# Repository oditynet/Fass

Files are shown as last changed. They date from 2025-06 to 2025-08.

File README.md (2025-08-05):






### FASS 
Robot on Arduino and servos with 2 degrees of freedom.

### Status 
  **PROJECT IN DEVELOPMENT**

The robot can now: walk forward and backward, lift 1 paw/2 paws/4 paws up, down, sideways, receive commands via radio from the remote control, understands the distance from lidars. An algorithm for turning in a circle is currently being developed.

### Theory
(next information is very hard)
Forward and inverse kinematics:
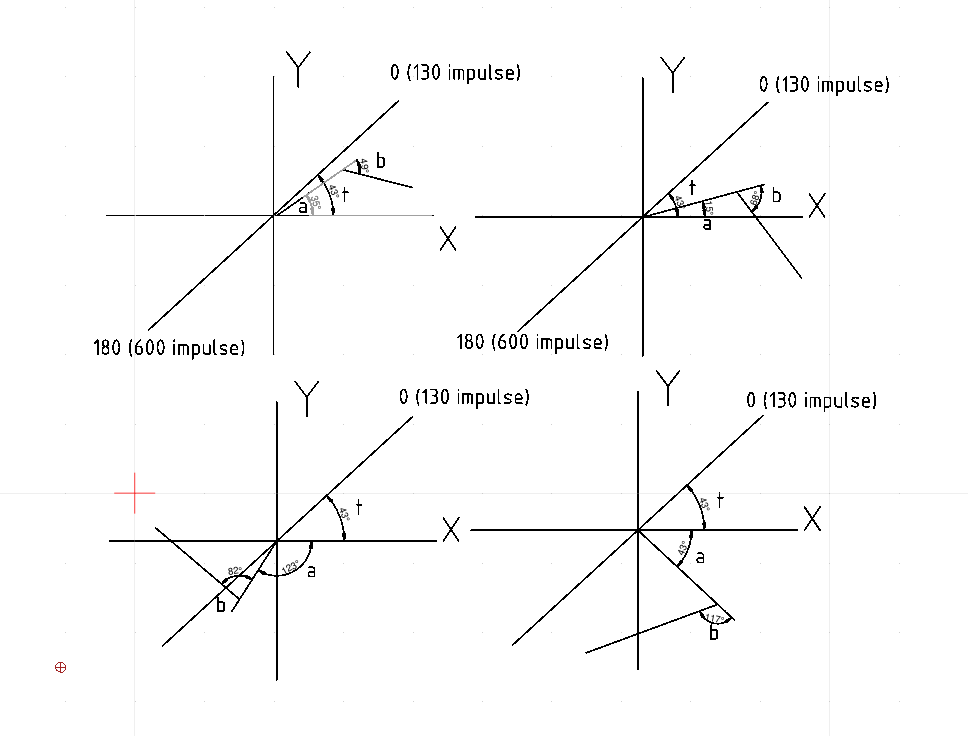
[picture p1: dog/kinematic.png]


Forward kinematics is knowing the impulses to find the coordinates of the end point X;Y.

For the first arm:

- x1 = L1 * cos(a);
- z1 = L1 * sin(a);

For the second arm. The minus sign is because the knee is pointing down and to get the second angle, you need to subtract from the first:

- x = x1 + L2 * cos((a - b));
- z = z1 + L2 * sin((a - b));

Inverse kinematics is to find angles (motor impulses) by X;Y coordinates. The graph shows 4 possible positions of the paw and therefore 4 different calculation methods. The angle t is always constant (equal to 45.5744 degrees), since the servo can rotate from 0 to 180 degrees (130 - 600 impulses) and for the motor this line is considered the abscissa. For the researcher, the abscissa is the X line. Arduino works with radians (1 rad = 57.29577 degrees) and therefore it is necessary to translate the values.

The same kinematics is for the movement of the paw to the side for turning. turning. walking sideways. The task is to find the angle y_c and to what height to compensate for the paw lift to the height z_H
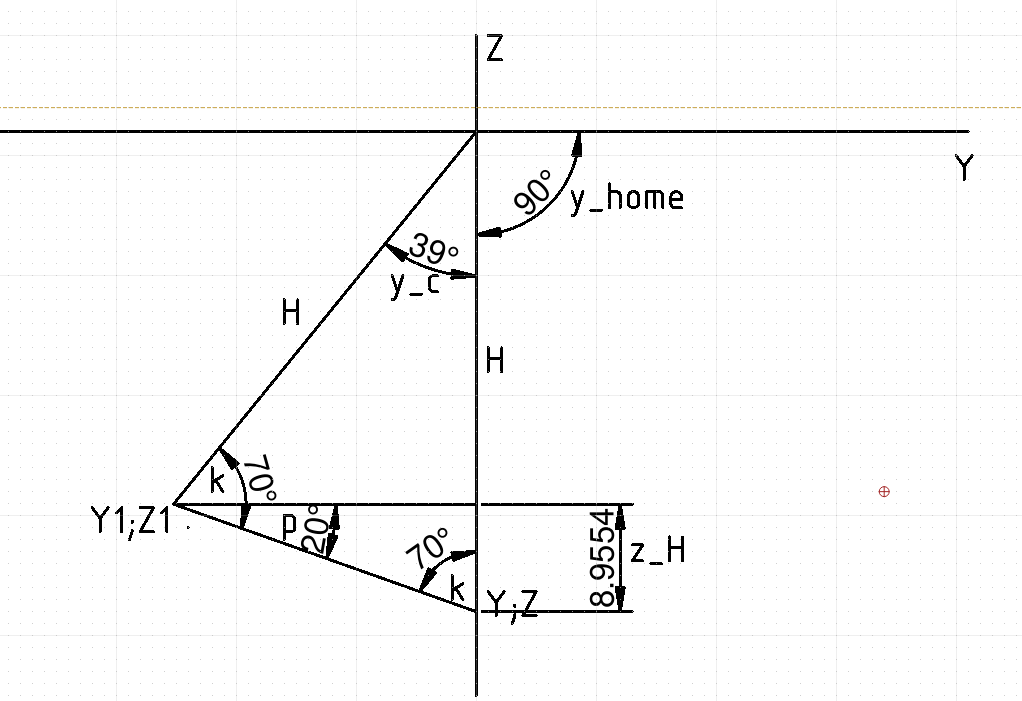
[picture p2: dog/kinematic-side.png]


### Step theory:

There are 2 types of steps in walking:

1) 2x2 - 1, 4 paws move forward at the same time and then 2, 3. The algorithm is successful when the dog's body is perfectly centered
2) 1x3 - the step cycle is divided into 4 stages (by the number of paws). The first paw moves forward in 1/4 of the period, and the other 3 continue to move backward. In the second period, 2/4, the second paw moves forward, and the others continue to move backward, and so on in a circle.

In my project, the center of gravity is unstable, so I chose option 2.

### HARDWARE LIST 
 1) Сервопривод SPT5435LV 35 кг                - 12 шт
 2) Понижающий регулятор напряжения на 10А     - 1 шт
 3) Arduino nano                               - 2 шт
 4) LM2596S-ADJ                                - 1 шт
 5) Подшипник фланцевый F688 ZZ                - 8 шт
 6) DS-212                                     - 5 шт
 7) KY-023                                     - 2 шт
 8) GY-521                                     - 1 шт
 9) HC-SR04                                    - 2 шт
 10) PCA9685                                   - 1 шт
 11) NRF24L01                                  - 2 шт
 12) LIPO 7.4V(ваш выбор) класс от 20С         - 2 шт
 13) болты и гайки M3                          - пакет на 100 шт

### Electrochema

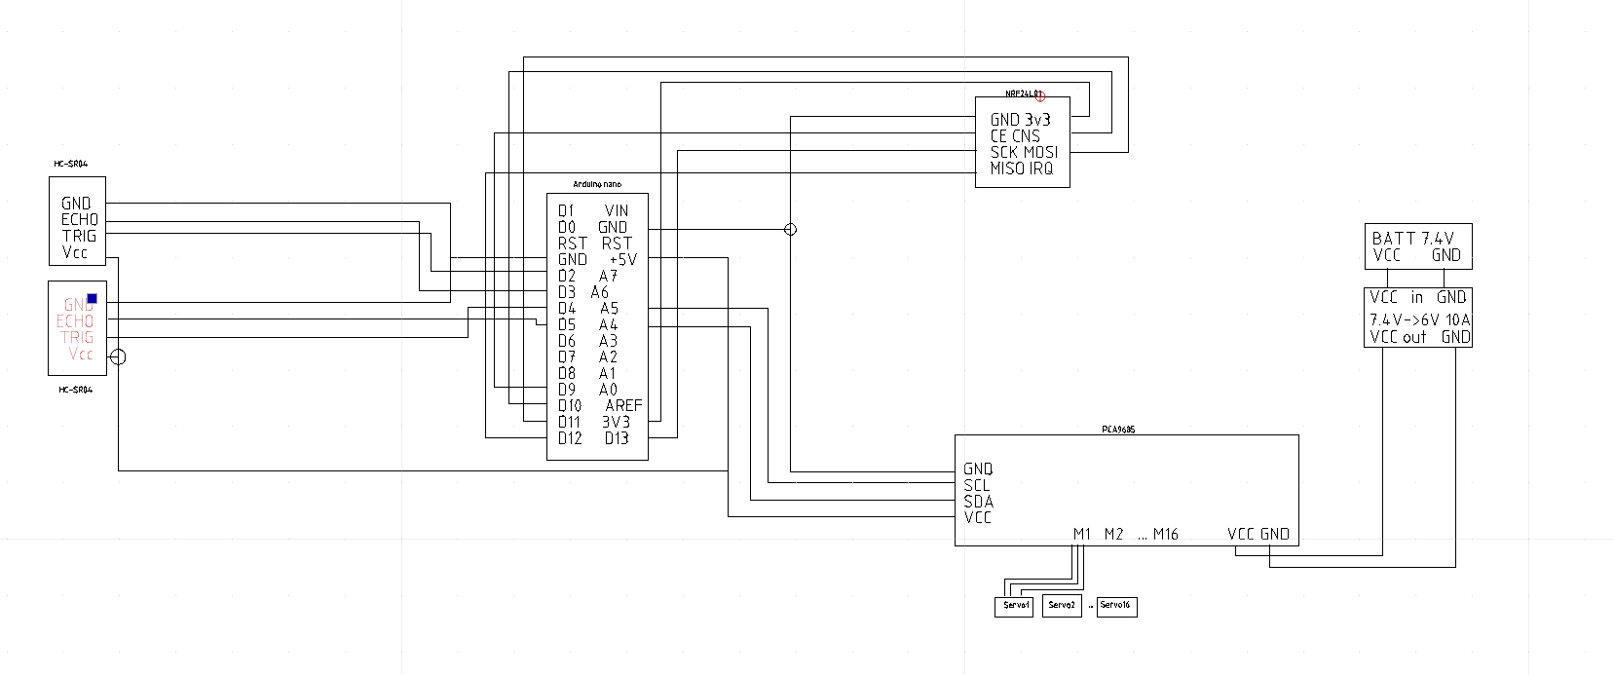
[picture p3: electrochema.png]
leg


### Video
  
Here is a video of the old kinematics motion logic. The new one works very accurately and takes into account all possible states.

leg

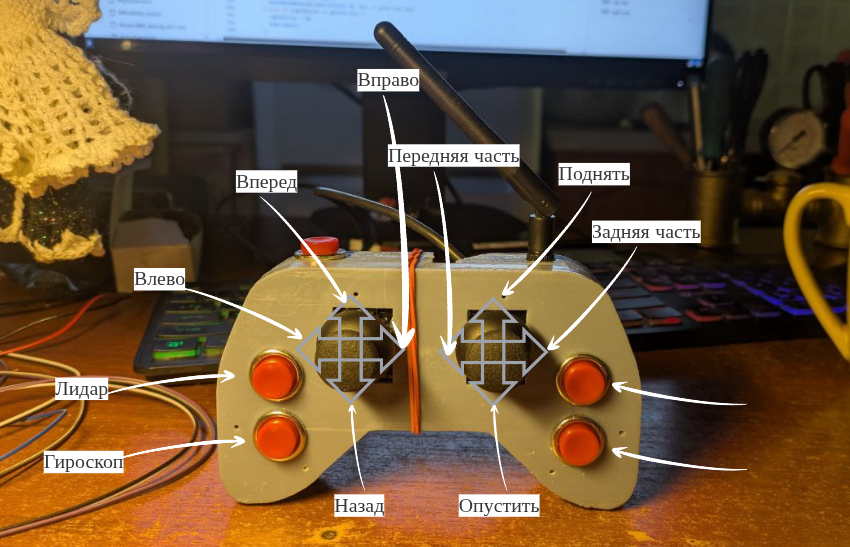
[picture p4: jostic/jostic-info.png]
jostic


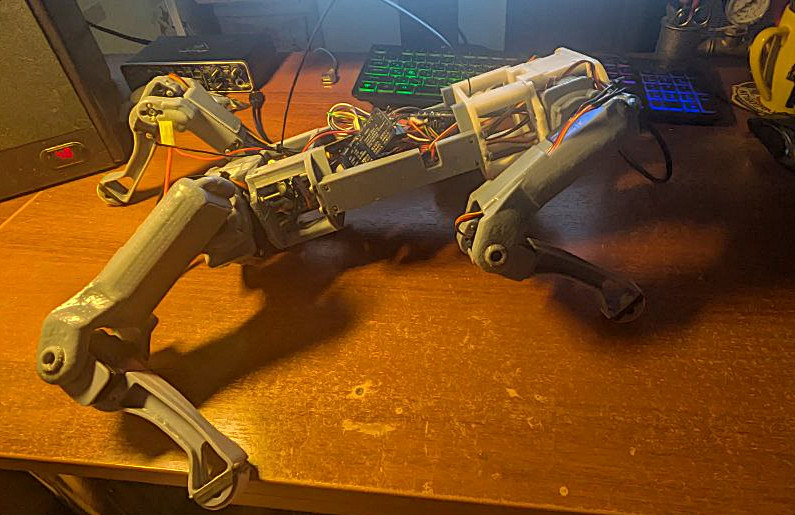
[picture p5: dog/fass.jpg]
fass


Main features of the implementation:
1) Control:
- Radio control via NRF24L01
- Automatic sensor priority
2) Movement algorithms:
- Smooth walking forward/backward
- Turns on the spot
- Automatic return to neutral position
- Adjustable movement speed
3) Inverse kinematics:
- Accurate calculation of joint angles
- Taking into account design constraints
- Smooth movement of legs
4) Safety system:
- Limiters for servos
- Smooth transitions between states

Hardware requirements:
- Arduino nano
- NRF24L01 module
- PCA9685 (servo driver)
- 12 servos (3 for each leg)
- MPU6050 (gyroscope / accelerometer)
- 2 HC-SR04 sensors (ultrasonic rangefinders)
- Remote control with two joysticks KY-023 and NRF24L01

origin project STL: https://novaspotmicro.com/parts-list.html with conversion to the metric system and my functionality. The software is written from scratch, inverse kinematics is developed and written from scratch. The algorithm is mine.

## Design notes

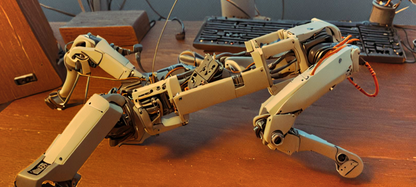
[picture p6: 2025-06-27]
head.png

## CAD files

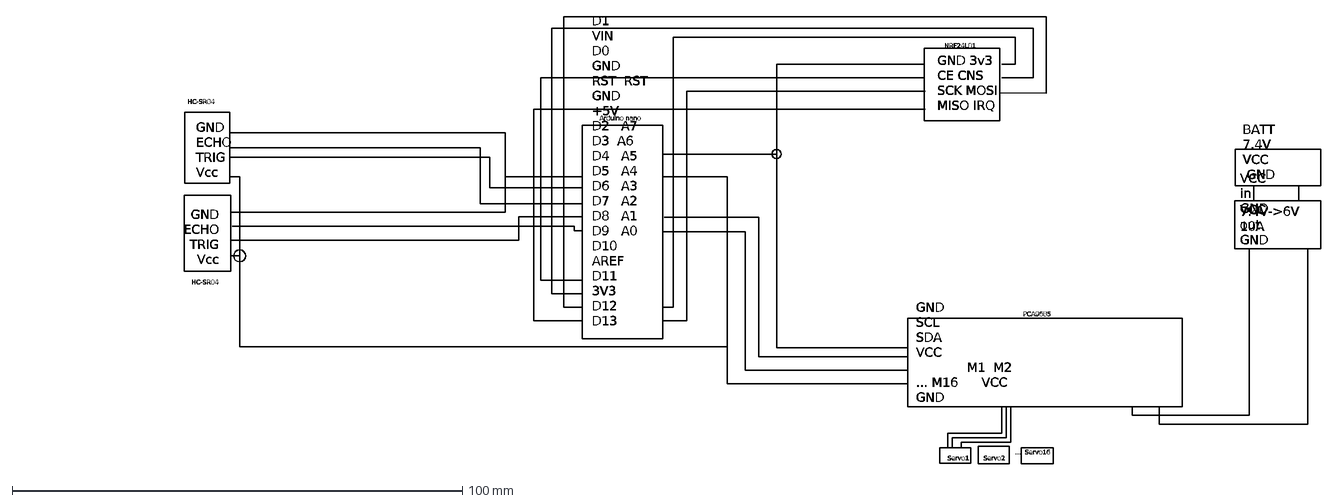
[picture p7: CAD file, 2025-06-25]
electrochema.dxf
D1\~\~\~ VIN D0\~ \~GND RST\~\~RST GND \~ +5V D2\~ \~A7 D3\~\~A6 D4\~ \~A5 D5\~ \~A4 D6\~ \~A3 D7\~ \~A2 D8\~ \~A1 D9\~ \~A0 D10\~ \~AREF D11\~ \~3V3 D12\~ \~D1
GND\~3v3 CE\~CNS SCK\~MOSI MISO\~IRQ
GND ECHO TRIG Vcc
GND SCL SDA VCC M1 M2 ... M16 VCC GND
Servo1
Servo2
... Servo16
BATT 7.4V VCC GND
7.4V->6V 10A
VCC in GND
VCC out GND
HC-SR04
Arduino nano
NRF24L01
PCA9685

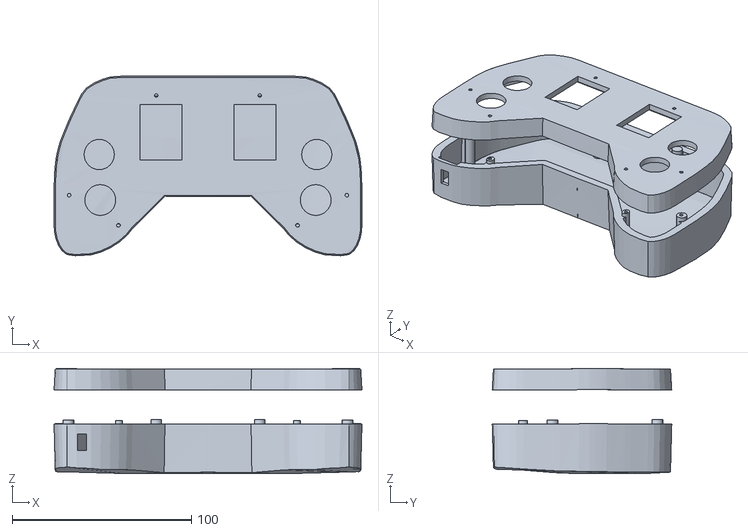
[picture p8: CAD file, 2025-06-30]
jostic/jostic-ver2.stl
171.7 x 100.1 x 58.6

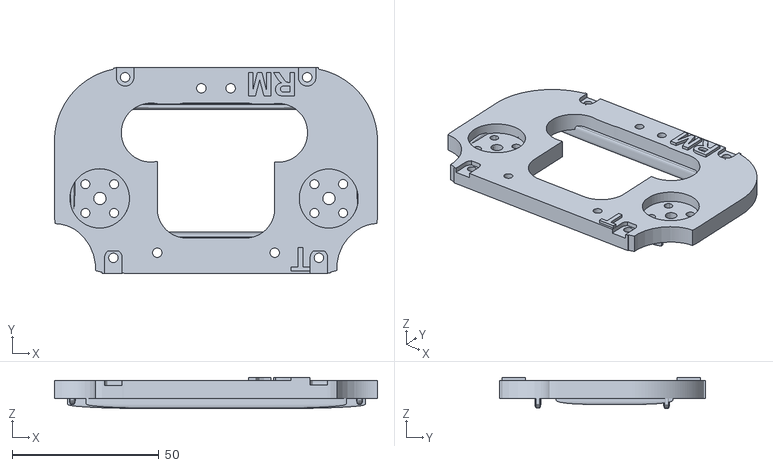
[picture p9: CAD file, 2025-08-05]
STL/G4-new.stl
110.0 x 70.0 x 10.6

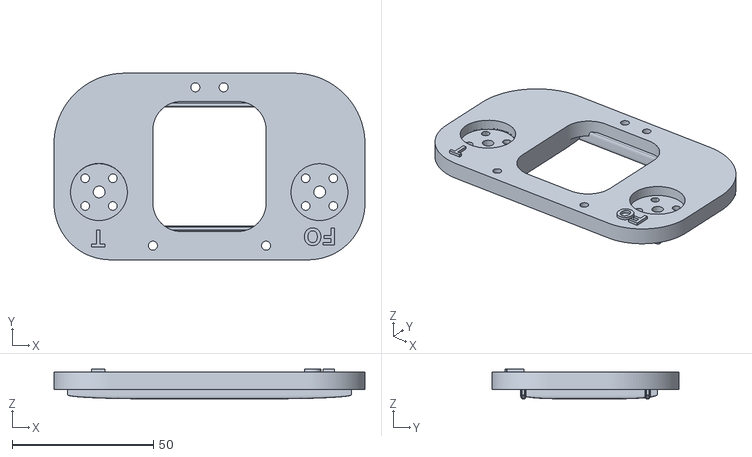
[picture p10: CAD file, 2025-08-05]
STL/G3-new.stl
110.0 x 66.0 x 10.5

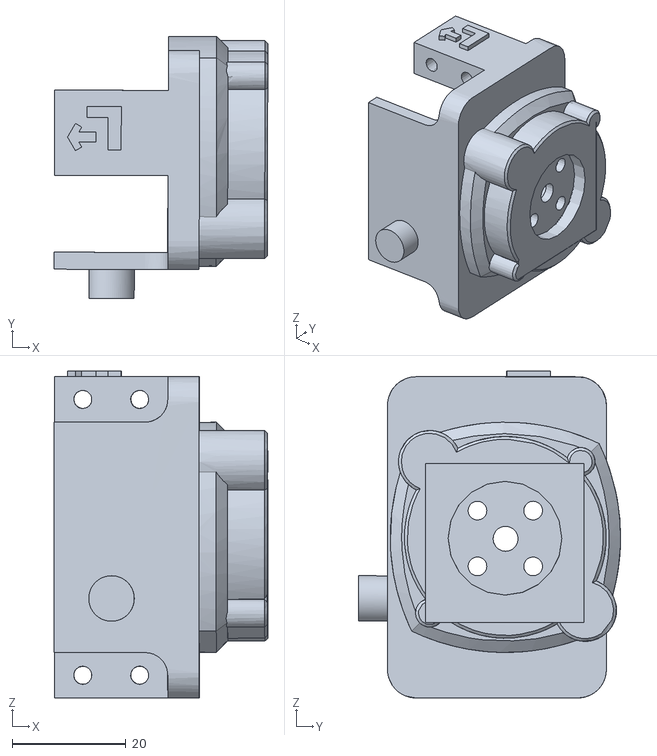
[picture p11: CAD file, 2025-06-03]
STL/SM3_Frame_LeftCoax-edit.stl
37.6 x 46.1 x 57.5

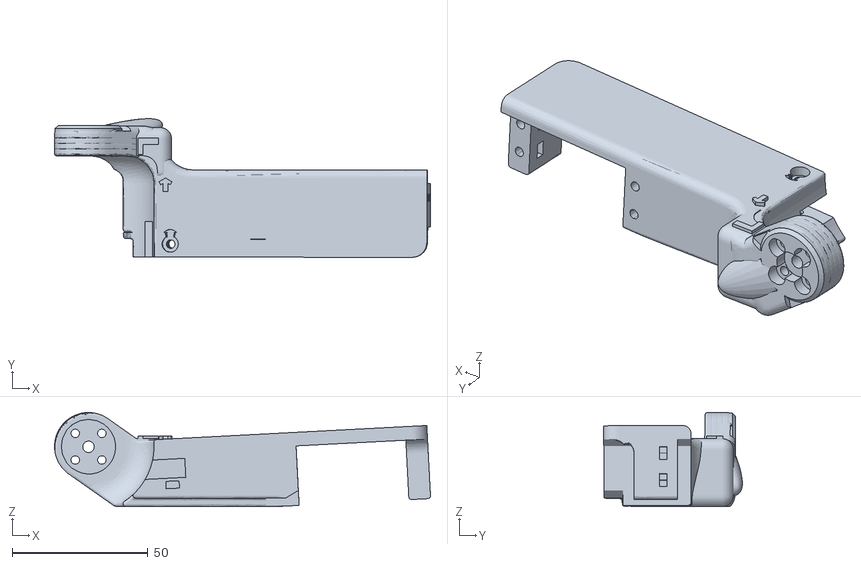
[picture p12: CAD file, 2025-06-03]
STL/SM3_Frame_LeftFemur-edit.stl
138.5 x 51.1 x 34.7

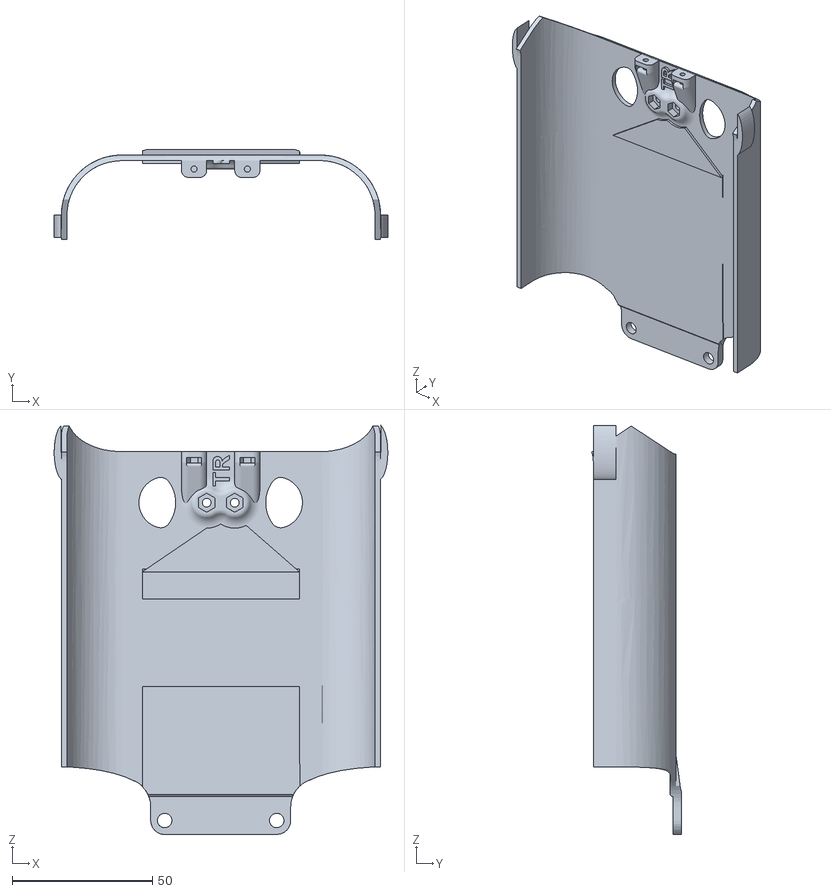
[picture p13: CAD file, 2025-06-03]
STL/SM3_Cover_TopRear.stl
119.1 x 32.1 x 146.0

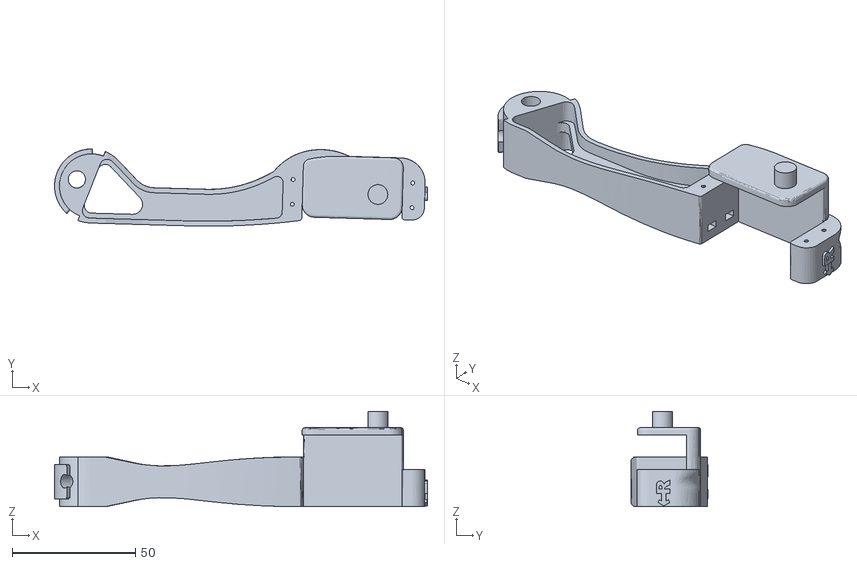
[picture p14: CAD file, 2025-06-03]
STL/SM3_Frame_RightTibia.stl
151.0 x 31.3 x 38.5

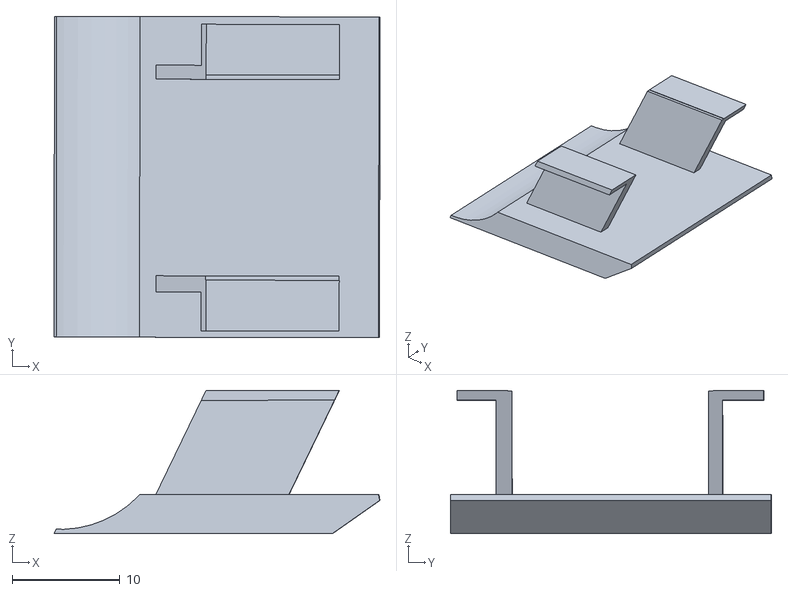
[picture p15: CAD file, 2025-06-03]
STL/SM3_Cover_HeadPanelSlug.stl
30.2 x 29.7 x 13.3

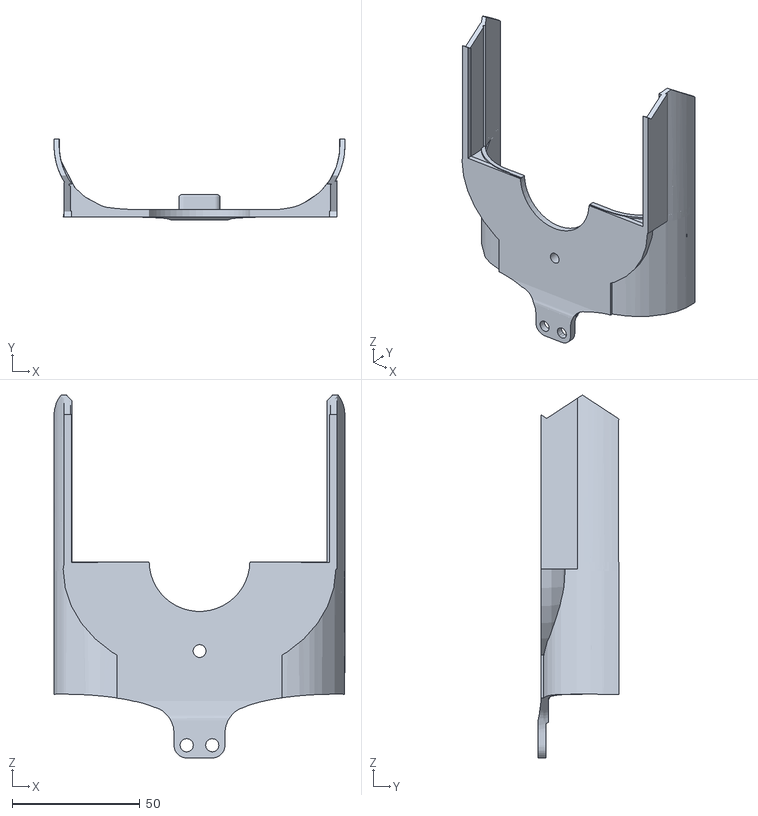
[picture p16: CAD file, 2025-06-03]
STL/SM3_Cover_BottomFront.stl
114.0 x 31.6 x 142.3

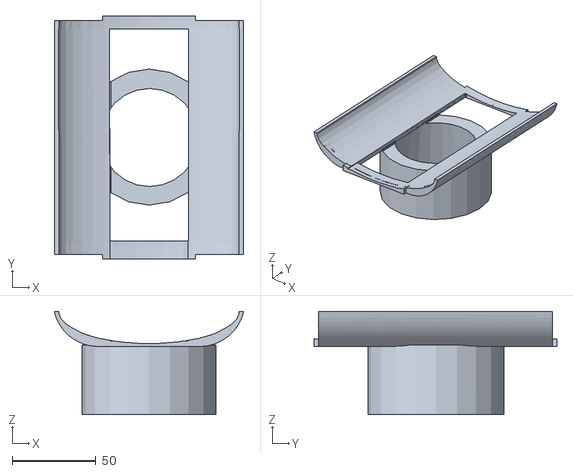
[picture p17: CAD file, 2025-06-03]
STL/SM3_Stand_ConeCap.stl
113.3 x 145.4 x 61.6

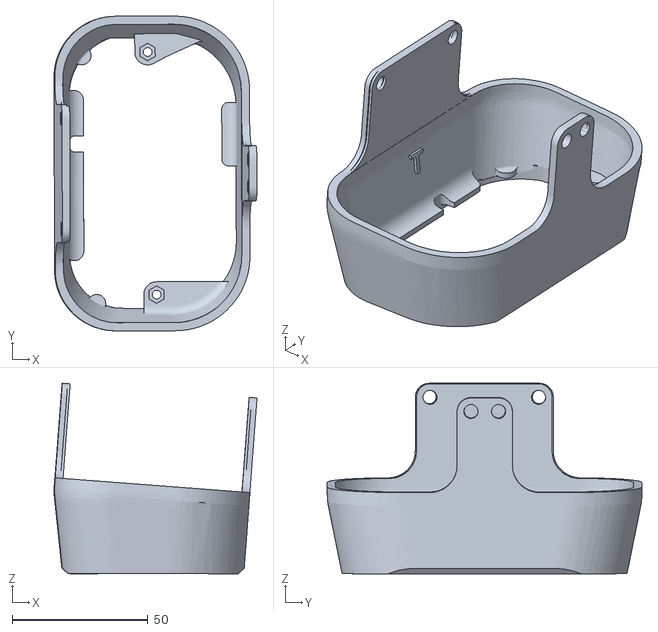
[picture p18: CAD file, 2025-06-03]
STL/SM3_Cover_RearPanel_2Piece_Shell.stl
74.8 x 116.1 x 70.2

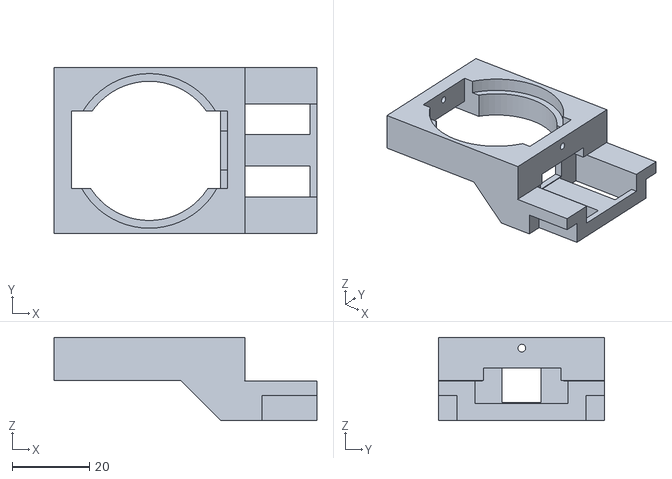
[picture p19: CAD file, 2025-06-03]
STL/SM3_Mp3ProSpeakerMount.stl
68.0 x 43.0 x 21.6

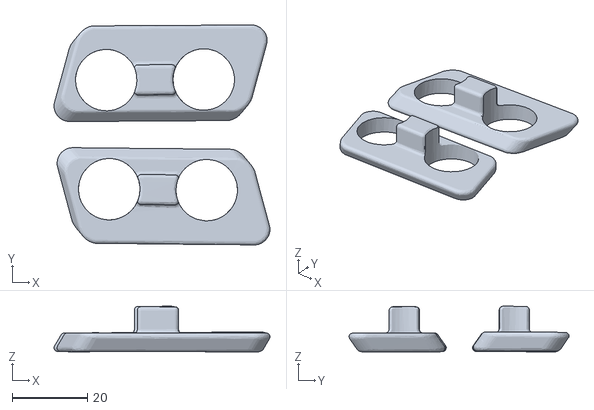
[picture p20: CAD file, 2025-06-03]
STL/SM3_Sensor_UltraSonicPlate.stl
57.6 x 58.6 x 12.2

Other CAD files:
STL/SM3_Cover_BottomHatch.stl
STL/SM3_Frame_FrontShoulderOuter.stl
STL/SM3_Sensor_PIRCup.stl
STL/SM3_Frame_FrontShoulderInner.stl
STL/SM3_Cover_BottomRear.stl
STL/SM3_Cover_LeftFemur.stl
STL/SM3_Cover_RearPanelBtnHolder_6x6LongBtn.stl
STL/SM3_Cover_RearPanel_2Piece_Base.stl
STL/SM3_Cover_RightFemur-edit.stl
STL/SM3_Cover_RightFemur.stl
STL/SM3_Cover_TopFront.stl
STL/SM3_Electronics_BuckConveterCase.stl
STL/SM3_Foot-edit.stl
STL/SM3_Foot.stl
STL/SM3_Frame_ChassisTrunk.stl
STL/SM3_Frame_FrontShoulderMiddle.stl
STL/SM3_Frame_LeftCoax.stl
STL/SM3_Frame_LeftFemur.stl
STL/SM3_Frame_LeftTibia.stl
STL/SM3_Frame_RearShoulderInner.stl
STL/SM3_Frame_RearShoulderMiddle.stl
STL/SM3_Frame_RearShoulderOuter.stl
STL/SM3_Frame_RightCoax.stl
STL/SM3_Frame_RightFemur.stl
STL/SM3_Sensor_FrontPIRMount.stl
STL/SM3_Sensor_MP3SpeakerMount.stl
STL/SM3_Sensor_RearPIRMount.stl
STL/SM3_Stand_ConeBase.stl

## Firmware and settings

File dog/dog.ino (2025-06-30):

//#include <Thread.h>  
#include <Wire.h>
#include <math.h>

#include <SPI.h>
#include <nRF24L01.h>
#include <RF24.h>

#include <Adafruit_PWMServoDriver.h>
Adafruit_PWMServoDriver pwm1 = Adafruit_PWMServoDriver();

#define TRIG1 2
#define ECHO1 3
#define TRIG2 5
#define ECHO2 4

// Конфигурация NRF24L01
#define CE_PIN   7
#define CSN_PIN 8


const byte thisSlaveAddress[4] = {'F','A','S','S'};
RF24 radio(CE_PIN, CSN_PIN);

// Структура для данных с пульта
struct RemoteData {
  int leftX;
  int leftY;
  int rightX;
  int rightY;
  int btn1;
  int btn2;
  int btn3;
  int btn4;
  int checksum; // Добавляем поле для контрольной суммы
};


//int spd = 50;

int L0 = 38;
int L1 = 108;
int L2 = 130;

int Lbody = 280;
int gotohome=0;

// Конфигурация сервоприводов
const int NUM_LEGS = 4;
const int NUM_JOINTS_PER_LEG = 3; // Плечо, бедро, колено
//const int FL = 0, FR = 1, RL = 2, RR = 3; // Индексы ног
//const int SHOULDER = 0, HIP = 1, KNEE = 2; // Индексы суставов

const int STEP_LENGTH = 40; //длина шага
const int STEP_HEIGHT = 30; //высота шага

//unsigned long previousMillis = 0;  // время хранения loop
//const long loop_interval = 500; // время проверки данных с джостика

const int legs[4][3][4] = {
  {{0, 130 ,600, 353}, {1, 130 ,600, 400}, {2,130, 600, 345}},   // FL плечо,бедро,локоть    
  {{4, 130 ,600, 335}, {5, 600 ,130, 347}, {6,600, 130, 379}},   // FR
  {{8, 130 ,600, 370}, {9, 130 ,600, 350}, {10,130, 600, 360}},   // RL
  {{12, 130 ,600, 372}, {13, 600 ,130, 385}, {14,600, 130, 360}}    // RR
};

float legspos[4][4] = { //X, Z, Height, Y
  {0, 0, 220, 0},  // FL   200 - примерно. надо вычислить home высоту TODO 
  {0, 0, 220, 0},  // FR
  {0, 0, 220, 0},  // RL
  {0, 0, 220, 0}   // RR
};

//Thread gefromjosticdata = Thread();

void step4legstoside(bool left, float STEP_DURATION, int Rcentr = 200);

float getDistance(int trigPin, int echoPin) {
  // Генерируем импульс 10 мкс
  digitalWrite(trigPin, LOW);
  delayMicroseconds(2);
  digitalWrite(trigPin, HIGH);
  delayMicroseconds(10);
  digitalWrite(trigPin, LOW);
  
  // Измеряем длительность импульса
  long duration = pulseIn(echoPin, HIGH);
  
  // Рассчитываем расстояние (см)
  //return duration * 0.034 / 2;
   return duration / 58;
}

int inverseLinearTransform(int value, int inMin = 0, int inMax = 400, int outMin = 200, int outMax = 1000) {
    // Ограничиваем входное значение в диапазоне [inMin, inMax]
    value = constrain(value, inMin, inMax);
    
    // Вычисляем преобразование с обратной линейностью
    return map(value, inMin, inMax, outMin, outMax);
}

void processRemoteData(RemoteData data) {
  // Движение вперед/назад/повороты
  int value;
  if (data.leftY < 400) {
    Serial.print("Y_up: "); Serial.println(data.leftY);

    value = inverseLinearTransform(data.leftY);
    gotohome=1;
    stepalllegs(false,value, 0 ); 
  } else if (data.leftY > 600) {
    Serial.print("Y_down: "); Serial.println(data.leftY);

    value = inverseLinearTransform(data.leftY, 600, 1024);
    gotohome=1;
    stepalllegs(true,value,0);
  } else if (data.leftX < 400) {
    Serial.print("X_up: "); Serial.println(data.leftX);

    value = inverseLinearTransform(data.leftX,0,400,1,40);
    gotohome=1;
    heightchange4leg(value); //LEft
  } else if (data.leftX > 600) {
    Serial.print("X_donwn: "); Serial.println(data.leftX);

    value = inverseLinearTransform(data.leftX,600, 1024, -1, -40);
    gotohome=1;
    heightchange4leg(value);//right
  } else if (abs(data.leftX - 512) < 100 && abs(data.leftY - 512) < 100) {
    
    if (gotohome == 1){
      Serial.println("Home: "); 
      //gohome();
      gotohome=0;
    }
  }
  if (data.rightX < 400) {
    Serial.print("R X_left: "); Serial.println(data.rightX);

    value = inverseLinearTransform(data.rightX);
    gotohome=1;
    step4legstoside(true, value); // Влево
  } else if (data.rightX > 600) {
    Serial.print("R X_right: "); Serial.println(data.rightX);
  
    value = inverseLinearTransform(data.rightX,600, 1024);
    gotohome=1;
    step4legstoside(false,  value); // Вправо
  }
}

void readRemoteData() {
  if (radio.available()) {
    RemoteData data;

    radio.read(&data, sizeof(data));

    int calculatedChecksum = data.checksum = data.leftX +data.leftY +data.rightX +data.rightY +data.btn1+data.btn2+data.btn3+data.btn4;
    if (data.checksum == calculatedChecksum && calculatedChecksum != 0) {
      
      Serial.println("Received raw data:");
      Serial.print("LX: "); Serial.print(data.leftX);
      Serial.print(" LY: "); Serial.print(data.leftY);
      Serial.print(" RX: "); Serial.print(data.rightX);
      Serial.print(" RY: "); Serial.print(data.rightY);
      Serial.print(" BTN: "); Serial.print(data.btn1);
      Serial.print(","); Serial.print(data.btn2);
      Serial.print(","); Serial.print(data.btn3);
      Serial.print(","); Serial.print(data.btn4);
      Serial.print(" Checksum: "); Serial.println(data.checksum);
      
      processRemoteData(data);
    }
  }
}

double realangleToPulse(double angle, int minPulse, int maxPulse, double minAngle = 0, double maxAngle = 180) {
    if (minPulse > maxPulse) {
        return maxPulse + (minPulse - maxPulse) * (1 - angle/180.0);
    }
    return minPulse + (maxPulse - minPulse) * (angle/180.0);
}

// Преобразование импульса в угол с учетом реального диапазона
double realpulseToAngle(int pulse, int minPulse, int maxPulse, double minAngle = 0, double maxAngle = 180) { 
    if (minPulse > maxPulse) {
        return 180.0 - 180.0 * (pulse - maxPulse) / (minPulse - maxPulse);
    }
    return 180.0 * (pulse - minPulse) / (maxPulse - minPulse);
}

void forwardKinematics(int leg,int hipPulse, int kneePulse, double &x, double &z) {
  double b = realpulseToAngle(kneePulse, legs[leg][2][1], legs[leg][2][2]);
  double a = realpulseToAngle(hipPulse, legs[leg][1][1], legs[leg][1][2]);

  //Serial.print("a=");Serial.print(a);Serial.print(" b=");Serial.println(b);
  //double P1 = (600-130)/180; //1 пульс = 2,61 градусам

  double b_Rad = radians(b);
  double a_Rad = radians(a);
  double x1,z1;
  
  a_Rad = radians(45.5744 - a);
  x1 = L1 * cos(a_Rad);
  z1 = L1 * sin(a_Rad);
  
  x = x1 + L2 * cos((a_Rad - b_Rad));
  z = z1 + L2 * sin((a_Rad - b_Rad));
  /*Serial.print("leg ");Serial.print(leg);
  Serial.print(" x1="); Serial.print(x1);
  Serial.print(" z1="); Serial.print(z1);
  Serial.print(" x=");  Serial.print(x); Serial.print(" z="); Serial.println(z);*/
}

bool inverseKinematics(int leg, double X, double Z, int &hipPulse, int &kneePulse) {
  double D = sqrt(X*X+Z*Z);
 // Serial.print("D=");Serial.println(D);
  if (D > L1 + L2 || D < abs(L1 - L2)) {
        Serial.println("Точка недостижима");
        return false;
  }
  double a,b,g,t,k;
  double _const =  45.5744;//(180/(600-130)) * (249-130);
  double MM_PI = 3.1415926;
  b = MM_PI - acos((L2*L2+L1*L1-D*D)/(2*L2*L1));

  if (X >= 0 && Z <= 0){ // 1 случай
   // Serial.println("[2]");
    t=acos((L1*L1-L2*L2+D*D)/(2*L1*D));
    k=acos(abs(X)/D);
    a = k-t+_const/57.29577; //+
  }
  else if (X >= 0 && Z >= 0){
    //Serial.println("[1]");
    k = acos(X/D);
    t = acos((L1*L1+D*D-L2*L2)/(2*L1*D));
    a = abs(_const/57.29577 - k - t);  //+
  }
  else if (X <= 0 && Z >= 0){
    //Serial.println("[4]");
    //a = MM_PI - acos((D*D + L1*L1 - L2*L2)/(2*L1*D)); //TODO кажется неверно ищится,т.к. весь треугольник не надо учитывать,раз у нас есть линия по 600 имп.
    a = /*90 гр перевел в рад*/1.57079632679 + (acos(abs(X)/D)) -  acos((D*D + L1*L1 - L2*L2)/(2*L1*D)); // перепроверить надо!!!!!
  }
  else if (X <= 0 && Z <= 0){
    //Serial.println("[3]");//Serial.println(MM_PI);Serial.println(PI);
    double k = acos(abs(X)/D);
    if (k * 57.29577 >= _const ) {// гр > гр
      //Serial.println("[3_1]");
     // Serial.println(k * 57.29577);
      a = MM_PI - (acos(abs(X)/D) - _const/57.29577) - acos((D*D + L1*L1 - L2*L2)/(2*L1*D));
    }else{
      //Serial.println("[3_2]");
      double kk = asin(abs(Z)/D);
      //a = kk-0.77537299217 ;
      a = MM_PI - (acos((D*D + L1*L1 - L2*L2)/(2*L1*D)) - kk + 0.77537299217); /*(90-45гр и в радианы перевел)*/
    }
    //double tmp = _const / 57.29577;
    //a = MM_PI - (acos(abs(X)/D) - (90 - _const)/57.29577) - acos((D*D + L1*L1 - L2*L2)/(2*L1*D));
    /*double theta = atan2(abs(X), abs(Z)); // Угол от отрицательной оси Z
    double cosGamma = (D*D + L1*L1 - L2*L2) / (2*L1*D);
    double gamma = acos(cosGamma);
    a = theta - gamma + _const/57.29577;*/
    //a = /*90 гр перевел в рад*/1.57079632679 + (acos(abs(X)/D)) -  acos((D*D + L1*L1 - L2*L2)/(2*L1*D));
  }
  else{
    Serial.println("[!] Not calculate");
    return false;
  }
  /*Serial.println("угол: ");
  Serial.println(a*57.29577);
  Serial.println(b*57.29577);
  */
  double rad_a = degrees(a);//-0.795423467); // это 45.5744 градусов
  double rad_b = degrees(b);

  kneePulse = realangleToPulse(rad_b, legs[leg][2][1], legs[leg][2][2]);
  hipPulse = realangleToPulse(rad_a, legs[leg][1][1], legs[leg][1][2]);
  return true;
}

void move1Leg(bool forward,int STEP_DURATION,double STEP_LENGTH,double STEP_HEIGHT , int servnum1, int servnum2 , int homeX, int homeZ,int leg) {

  const int NUM_STEPS = 25;        // Количество промежуточных точек
  double x,z;
  for (int i = 0; i <= NUM_STEPS; i++) {
    double t = (double)i / NUM_STEPS;
    
    // Фаза переноса (ПОДЪЕМ ноги)
    if (forward) {
      x = homeX + STEP_LENGTH * (1 - cos(PI * t)) ;
    } else {
      x = homeX - STEP_LENGTH * (1 - cos(PI * t)) ;
    }
    z = homeZ + STEP_HEIGHT * sin(PI * t); 
    
    // Отладочный вывод
    /*Serial.print("Target: X="); Serial.print(x);
    Serial.print(" Z="); Serial.println(z);
    moveToPoint(leg,x,z,servnum1,servnum2);*/

    delay(STEP_DURATION / (2 * NUM_STEPS));
  }
  double tmp;
  if (x > homeX) {
    tmp =  x - homeX;
  } else {
    tmp = homeX - x;
  }
  //2 фаза: возврат назад
  for (int i = 0; i <= NUM_STEPS; i++) {
   
    if (forward) {
      x = x - tmp / NUM_STEPS;
    } else {
      x = x + tmp / NUM_STEPS; 
    }

   /* Serial.print("Target: X="); Serial.print(x);
    Serial.print(" Z="); Serial.println(z);
*/
    moveToPoint(leg,x,z,servnum1,servnum2);
    delay(STEP_DURATION / (2 * NUM_STEPS));
  }
}

bool moveToPoint(int leg,double targetX, double targetZ, int servnum1, int servnum2 ) {
  int hipPulse, kneePulse;

 // Serial.println(targetZ);
  
  if (inverseKinematics(leg,targetX, targetZ, hipPulse, kneePulse)) {
    // Управление сервоприводами
    pwm1.setPWM(servnum1, 0, hipPulse);
    pwm1.setPWM(servnum2, 0, kneePulse);
    return true;
  } else {
    Serial.println("Ошибка перемещения");
  }
  return false;
}


void stepalllegs(bool forward,int speed, int left){ // left ^ 0- forward, 1- left, 2- right
 /* if (left == 1 || left ==0 ){
    step2legs(forward,0,3, legspos[0][0], legspos[0][1], legspos[3][0], legspos[3][1], speed); //
    step2legs(forward,1,2, legspos[1][0], legspos[1][1], legspos[2][0], legspos[2][1], speed); // поворот налево только
  }
  if (left == 1 || left == 0){
    step2legs(forward,1,2, legspos[1][0], legspos[1][1], legspos[2][0], legspos[2][1], speed);
    step2legs(forward,0,3, legspos[0][0], legspos[0][1], legspos[3][0], legspos[3][1], speed); 
  }*/
}
/*
void step2legs(bool forward, int legF, int legR, int homeX, int homeZ, int homeX1, int homeZ1,int STEP_DURATION){
  const int NUM_STEPS = 30;        // Количество промежуточных точек
  const int delta = 2;        // Разница можду шагаме переда и зада
  double x,z,x1,z1, t, t1;
  for (int i = 0; i <= NUM_STEPS+delta; i++) {
    if (i<= NUM_STEPS){
      t = (double)i / NUM_STEPS;

      if (forward) {
        x = homeX + STEP_LENGTH * (1 - cos(PI * t)) / 2;
      } else {
        x = homeX - STEP_LENGTH * (1 - cos(PI * t)) / 2;
      }
      z = homeZ + STEP_HEIGHT * sin(PI * t)/2; 
      moveToPoint(legF, x, z , legs[legF][1][0] , legs[legF][2][0]);

      legspos[legF][0] = x;
      legspos[legF][1] = z;
    }
    if (i >= delta){
      t1 = (double)(i-delta) / NUM_STEPS;

      if (forward) {
        x1 = homeX1 + STEP_LENGTH * (1 - cos(PI * t1)) / 2;
      } else {
        x1 = homeX1 - STEP_LENGTH * (1 - cos(PI * t1)) / 2;
      }
      z1 = homeZ1 + STEP_HEIGHT * sin(PI * t1)/2; 

      moveToPoint(legR, x1, z1 , legs[legR][1][0] , legs[legR][2][0]);
      
      legspos[legR][0] = x1;
      legspos[legR][1] = z1;
    }
    delay(STEP_DURATION / (2 * NUM_STEPS));
  }
  double tmp;
  if (x > homeX) {
    tmp =  x - homeX;
  } else {
    tmp = homeX - x;
  }
  //2 фаза: возврат назад
  for (int i = 0; i <= NUM_STEPS; i++) {
   
    if (forward) {
      x = x - tmp / NUM_STEPS;
    } else {
      x = x + tmp / NUM_STEPS; 
    }
    moveToPoint(x,z);
    delay(STEP_DURATION / (2 * NUM_STEPS));
  }
}
*/
int changeleg(int leg) {
    const int nextLeg[] = {2, 3, 1, 0}; // 0->2, 1->3, 2->1, 3->0
    return nextLeg[leg];
}
int changeleg0312(int leg) {
    const int nextLeg[] = {3, 2, 0, 1}; // 0->2, 1->3, 2->1, 3->0
    return nextLeg[leg];
}

void step4legs(bool forward, int STEP_DURATION, int len4step = 150) {
    const int NUM_SECTIONS = 4;
    const int STEPS_PER_SECTION = 10; // Фиксированное количество шагов на секцию
    const float SECTION_DURATION = STEP_DURATION / (float)NUM_SECTIONS;
    const float TIME_PER_STEP = SECTION_DURATION / STEPS_PER_SECTION;
    const float SECTION_LENGTH = len4step / (float)NUM_SECTIONS;

    int active_leg = 0; // Начинаем с ноги 0
    float start_positions[4][2]; // Стартовые позиции для всех ног

    for (int section = 0; section < NUM_SECTIONS; section++) {
        // Сохраняем стартовые позиции для всех ног
        for (int l = 0; l < 4; l++) {
            start_positions[l][0] = legspos[l][0];
            start_positions[l][1] = legspos[l][1];
        }

        for (int step = 0; step <= STEPS_PER_SECTION; step++) {
            float t = (float)step / STEPS_PER_SECTION; // Прогресс [0, 1]

            // Обработка ВСЕХ ног
            for (int l = 0; l < 4; l++) {
                if (l == active_leg) {
                    // Траектория активной ноги (полуэллипс)
                    float x, z;
                    if (forward) {
                        x = start_positions[l][0] + SECTION_LENGTH * t;
                    } else {
                        x = start_positions[l][0] - SECTION_LENGTH * t;
                    }
                    z = start_positions[l][1] + STEP_HEIGHT * sin(PI * t);
                    moveToPoint(l, x, z, legs[l][1][0], legs[l][2][0]);
                    legspos[l][0] = x;
                    legspos[l][1] = z;
                    delay(TIME_PER_STEP/(4*10));//быстрее
                } else {
                    // Траектория опорных ног (прямая с компенсацией)
                    float compensation = (forward ? -1 : 1) * SECTION_LENGTH * t / 3.0f;
                    float x = start_positions[l][0] + compensation;
                    moveToPoint(l, x, start_positions[l][1], legs[l][1][0], legs[l][2][0]);
                    // Не обновляем legspos здесь - только в конце секции
                    delay(TIME_PER_STEP/4);
                }
            }
            //delay(TIME_PER_STEP);
        }

        // Финализируем позиции после секции
        for (int l = 0; l < 4; l++) {
            if (l != active_leg) {
                float compensation = (forward ? -1 : 1) * SECTION_LENGTH / 3.0f;
                legspos[l][0] = start_positions[l][0] + compensation;
            }
        }

        // Логирование после каждой секции
        Serial.print("End section ");
        Serial.print(section);
        Serial.print(" - ");
        for (int l = 0; l < 4; l++) {
            Serial.print("Leg");
            Serial.print(l);
            Serial.print(": ");
            Serial.print(legspos[l][0]);
            Serial.print(" ");
        }
        Serial.println();

        // Переключаем активную ногу
        active_leg = changeleg(active_leg);
    }
}

void step1legtoside(bool left, int leg,int len){  // work!!
  double ab = (left ? 1 : -1)*(atan(len/abs(legspos[leg][1])) + atan((L1+L2)/L0));
  Serial.println(ab);
  //double rad_ab = degrees(ab);
  double shoulder = realangleToPulse(degrees(ab), legs[leg][0][1], legs[leg][0][2]);// +(left ? 1 : -1)*legs[leg][0][3];
  Serial.println(shoulder);
  pwm1.setPWM(legs[leg][0][0], 0, shoulder);
}
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
void loop() {

  //for (int i=0;i< 10;i++){
  //step4legstoside(true, 1000); 
  //}
  //gohome();
  readRemoteData();
  delay(500);

  /*float dist1 = getDistance(TRIG1, ECHO1);
  float dist2 = getDistance(TRIG2, ECHO2);
  Serial.print("Left: ");
  Serial.print(dist1);
  Serial.print(" cm | Right: ");
  Serial.print(dist2);
  Serial.println(" cm");
  delay(200);
*/
  /*for (int i=0;i< 10;i++){
  delay(7);
  step4legs(false,700); // технология 1х3
  }
  for (int i=0;i< 10;i++){
  delay(7);
  step4legs(false,400); // технология 1х3
  }
  for (int i=0;i< 10;i++){
  delay(7);
  step4legs(false,200); // технология 1х3
  }*/
  //stepalllegs(false,1000,0); // технология 2х2
//move1Leg(false,30,80,40 ,5,6 , legspos[3][0], legspos[3][1],3);
  //if (gefromjosticdata.shouldRun())
   //     gefromjosticdata.run();
  /*  АНАЛОГ
  unsigned long currentMillis = millis(); 
  if (currentMillis - previousMillis >= loop_interval){
     previousMillis = currentMillis;
     // чтение данных с джостика
  }*/
  

}

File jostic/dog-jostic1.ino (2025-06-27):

#include <SPI.h>
#include <nRF24L01.h>
#include <RF24.h>

// Конфигурация NRF24L01
#define CE_PIN   7
#define CSN_PIN 8
const byte slaveAddress[4] = {'F','A','S','S'};
RF24 radio(CE_PIN, CSN_PIN); // Create a Radio

// Пины джойстиков
const int LEFT_JOYSTICK_X = A2;
const int LEFT_JOYSTICK_Y = A3;
const int RIGHT_JOYSTICK_X = A0;
const int RIGHT_JOYSTICK_Y = A1;

struct RemoteData {
  int leftX;
  int leftY;
  int rightX;
  int rightY;
  int btn1;
  int btn2;
  int btn3;
  int btn4;
  int checksum; // Добавляем поле для контрольной суммы
};

// Параметры калибровки
const int NEUTRAL_ZONE = 50;  // Зона нечувствительности
const int MIN_THRESHOLD = 400; // Нижний порог активации
const int MAX_THRESHOLD = 600; // Верхний порог активации

const int button1 = 3;
const int button2 = 2;
const int button3 = 6;
const int button4 = 5;

// Таймер для отправки данных
unsigned long lastSendTime = 0;
const int SEND_INTERVAL = 500; // Интервал отправки (мс)

void setup() {
  Serial.begin(115200);
  Serial.println("Инициализация пульта управления...");
  
  // Настройка пинов джойстиков
  pinMode(LEFT_JOYSTICK_X, INPUT);
  pinMode(LEFT_JOYSTICK_Y, INPUT);
  pinMode(RIGHT_JOYSTICK_X, INPUT);
  pinMode(RIGHT_JOYSTICK_Y, INPUT);

    radio.begin();
    radio.setDataRate( RF24_250KBPS );
    //radio.setRetries(1,1); // delay, count
    radio.openWritingPipe(slaveAddress);
    radio.setChannel(98);
     radio.setAutoAck(true);
  
  while (!radio.isChipConnected()) {
    Serial.println("Ошибка: nRF24L01 не подключен!");
    delay(1000);
  }
  
  pinMode(button1, INPUT_PULLUP);
  pinMode(button2, INPUT_PULLUP);
  pinMode(button3, INPUT_PULLUP);
  pinMode(button4, INPUT_PULLUP);

  Serial.println("Пульт готов к работе");
}

void loop() {
  // Чтение значений с джойстиков
  RemoteData data;
  
  // Отправка данных с заданным интервалом
  if (millis() - lastSendTime >= SEND_INTERVAL) {
    data.leftX = analogRead(LEFT_JOYSTICK_X);
    data.leftY = analogRead(LEFT_JOYSTICK_Y);
    data.rightX = analogRead(RIGHT_JOYSTICK_X);
    data.rightY = analogRead(RIGHT_JOYSTICK_Y);
    

    data.btn1 = !digitalRead(button1); // Инвертируем, так как INPUT_PULLUP
    data.btn2 = !digitalRead(button2);
    data.btn3 = !digitalRead(button3);
    data.btn4 = !digitalRead(button4);

    applyCalibration(data);

    // Вычисление контрольной суммы
    data.checksum = data.leftX +data.leftY +data.rightX +data.rightY +data.btn1+data.btn2+data.btn3+data.btn4;

    bool result = radio.write(&data, sizeof(data));
    if (result) {
        Serial.println("[+]");
    }
    else {
        Serial.print("-");
    }


    lastSendTime = millis();
  }
  
  // Вывод значений в Serial для отладки
  static unsigned long lastPrintTime = 0;
  if (millis() - lastPrintTime > 500) {
    printJoystickData(data);
    lastPrintTime = millis();
  }
  delay(300);
}

// Применение калибровки и зоны нечувствительности
void applyCalibration(RemoteData &data) {
  // Левый джойстик (движение)
  data.leftX = mapAndFilter(data.leftX);
  data.leftY = mapAndFilter(data.leftY);
  
  // Правый джойстик (высота)
  data.rightX = mapAndFilter(data.rightX);
  data.rightY = mapAndFilter(data.rightY);
}

// Фильтрация значений и преобразование в диапазон 0-1023
int mapAndFilter(int value) {
  // Применение зоны нечувствительности
  if (abs(value - 512) < NEUTRAL_ZONE) {
    return 512; // Нейтральное положение
  }
  return value;
}

// Вывод данных джойстиков в Serial
void printJoystickData(RemoteData data) {
  Serial.print("Левый X: ");
  Serial.print(data.leftX);
  Serial.print(" Y: ");
  Serial.print(data.leftY);
  
  Serial.print(" | Правый X: ");
  Serial.print(data.rightX);
  Serial.print(" Y: ");
  Serial.print(data.rightY);
  
  // Расшифровка команд
  Serial.print(" | Команда: ");
  
  // Движение
  if (data.leftY < MIN_THRESHOLD) {
    Serial.print("ВПЕРЕД ");
  } else if (data.leftY > MAX_THRESHOLD) {
    Serial.print("НАЗАД ");
  }
  
  if (data.leftX < MIN_THRESHOLD) {
    Serial.print("ВЛЕВО ");
  } else if (data.leftX > MAX_THRESHOLD) {
    Serial.print("ВПРАВО ");
  }
  
  // Управление высотой
  if (data.rightY < MIN_THRESHOLD) {
    if (data.rightX < MIN_THRESHOLD) {
      Serial.print("ПОДНЯТЬ ПЕРЕД ");
    } else if (data.rightX > MAX_THRESHOLD) {
      Serial.print("ПОДНЯТЬ ЗАД ");
    } else {
      Serial.print("ПОДНЯТЬ ВСЕ ");
    }
  } else if (data.rightY > MAX_THRESHOLD) {
    if (data.rightX < MIN_THRESHOLD) {
      Serial.print("ОПУСТИТЬ ПЕРЕД ");
    } else if (data.rightX > MAX_THRESHOLD) {
      Serial.print("ОПУСТИТЬ ЗАД ");
    } else {
      Serial.print("ОПУСТИТЬ ВСЕ ");
    }
  }
  
  if (data.leftX >= MIN_THRESHOLD && data.leftX <= MAX_THRESHOLD && 
      data.leftY >= MIN_THRESHOLD && data.leftY <= MAX_THRESHOLD &&
      data.rightY >= MIN_THRESHOLD && data.rightY <= MAX_THRESHOLD) {
    Serial.print("СТОП");
  }
  
  Serial.println();
}

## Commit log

2025-06-12 Add 4 a buttons
2025-06-15 ver 0.1
    корректно работает шаг вперед и назад
2025-06-17 for test: изменение высот, ходьба
2025-06-17 for test
    умеет ходить, менять высоту. Реализовал параллелизм, чтоб не завивать задержками с джостика
2025-06-17 go home из любой точки
2025-06-17 jostic v3
    [Untitled.blend]
2025-06-18 Тестовая версия 0.1. Ходит, но как контуженный
2025-06-19 fix all bugs in ver 0.1
    [dog1.ino]
2025-06-22 ver 0.1 1х3
2025-06-23 добавил подъем ноги в сторону. ver 0.1
2025-06-23 добавил лидар
2025-06-25 electrochema v0.1
    [electrochema.dxf]
2025-06-30 release 0.1
    [Untitled.blend, jostic-ver2.stl]
